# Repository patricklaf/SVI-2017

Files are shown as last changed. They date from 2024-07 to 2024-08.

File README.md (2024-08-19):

# SVI-2017

English - [Français](LISEZMOI.md)

The SVI-2017 board is the recreation of the interface board for the RobotArm SVI 2000.

The functional board in version 1.1 is compatible with MSX computers.

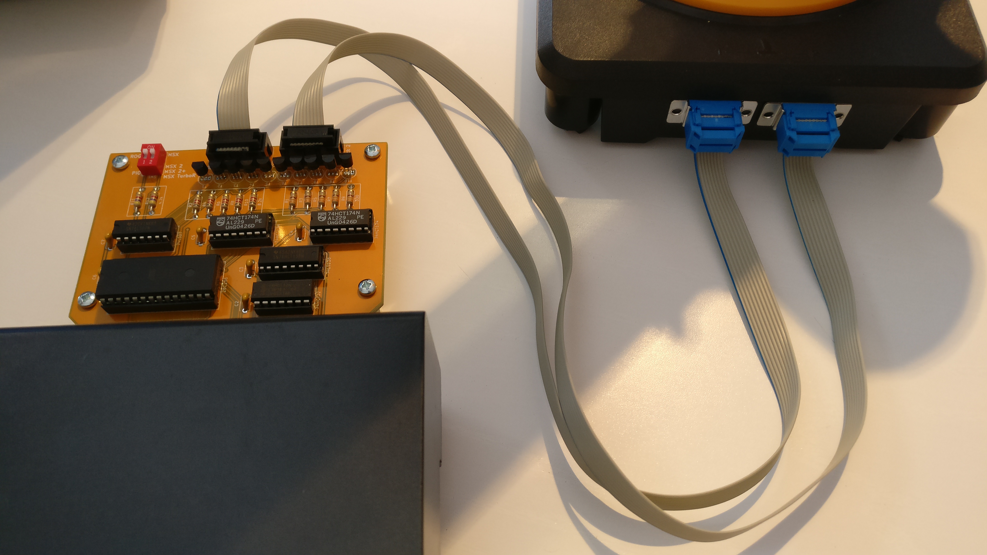
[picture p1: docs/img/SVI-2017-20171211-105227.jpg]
SVI-2017


## KiCad Project

The original project dates from 2017.

The [KiCad](KiCad/) folder contains the project migrated to KiCad 8.0.4.

The original archive [SVI-2017-201711091030.zip](https://github.com/patricklaf/SVI-2017/raw/main/KiCad/Gerber/SVI-2017-201711091030.zip) contains the Gerber files needed to produce the PCB. The build has been successfully tested by [Seeedstudio](https://www.seeedstudio.com/fusion_pcb.html).

An [interactive BOM](https://patricklaf.github.io/SVI-2017/bom.html) is available to view the list of required components and help with assembly.

You can order PCB directly from shared project on PCBWay.

<a href="https://www.pcbway.com/project/shareproject/SVI_2017_board_b98df38c.html">PCB from PCBWay</a>

## ROM

The [ROGO.ROM](https://github.com/patricklaf/SVI-2017/raw/main/ROM/ROGO.ROM) file is the image needed to program the EEPROM of the board.

The file combines the following elements:

- The ROGO ROM for MSX.
- The modified ROGO ROM for MSX 2, MSX 2+ and MSX TurboR.

## Usage

The DIP switch on the board selects the operating mode of the board.

Switch 1 selects the ROGO ROM or PIO mode.

Switch 2 selects the model of the computer used to activate the compatible ROM.

## ROGO

The ROGO language, similar to the Logo language, allows the robot to be controlled using commands.

A drawing of the robot on the screen reproduces the movements made.

## PIO

In PIO mode, the robot's movements are made by directly activating the motors, in one direction or another. Ports 0 and 1 are used. A movement is activated by setting the corresponding bit to 1. The movement stops when the bit is set to 0.

Port 0

| Bit | Movement |
|:---:|:---|
| 0 | Axis 2, arm forward |
| 1 | Axis 2, arm back |
| 2 | Axis 1, left rotation  |
| 3 | Axis 1, right rotation |
| 4 | Axis 5, clamp closing  |
| 5 | Axis 5, clamp opening  |

Port 1

| Bit | Movement |
|:---:|:---|
| 0 | Axis 3, arm down |
| 1 | Axis 3, arm up |
| 2 | Axis 1, clamp rotation left  |
| 3 | Axis 1, clamp rotation right |

> [!CAUTION]
> Never activate the 2 movements of an axis simultaneously, otherwise you risk damaging the electronics of the card.

## Acknowledgments

This project could not have been completed without the invaluable help of the members of the [MSX Village](https://msxvillage.fr) website.

There is a dedicated topic on the site's forum: [Robotarm SVI the diagram](https://msxvillage.fr/forum/topic-326-1+robotarm-svi-le-schema.php).

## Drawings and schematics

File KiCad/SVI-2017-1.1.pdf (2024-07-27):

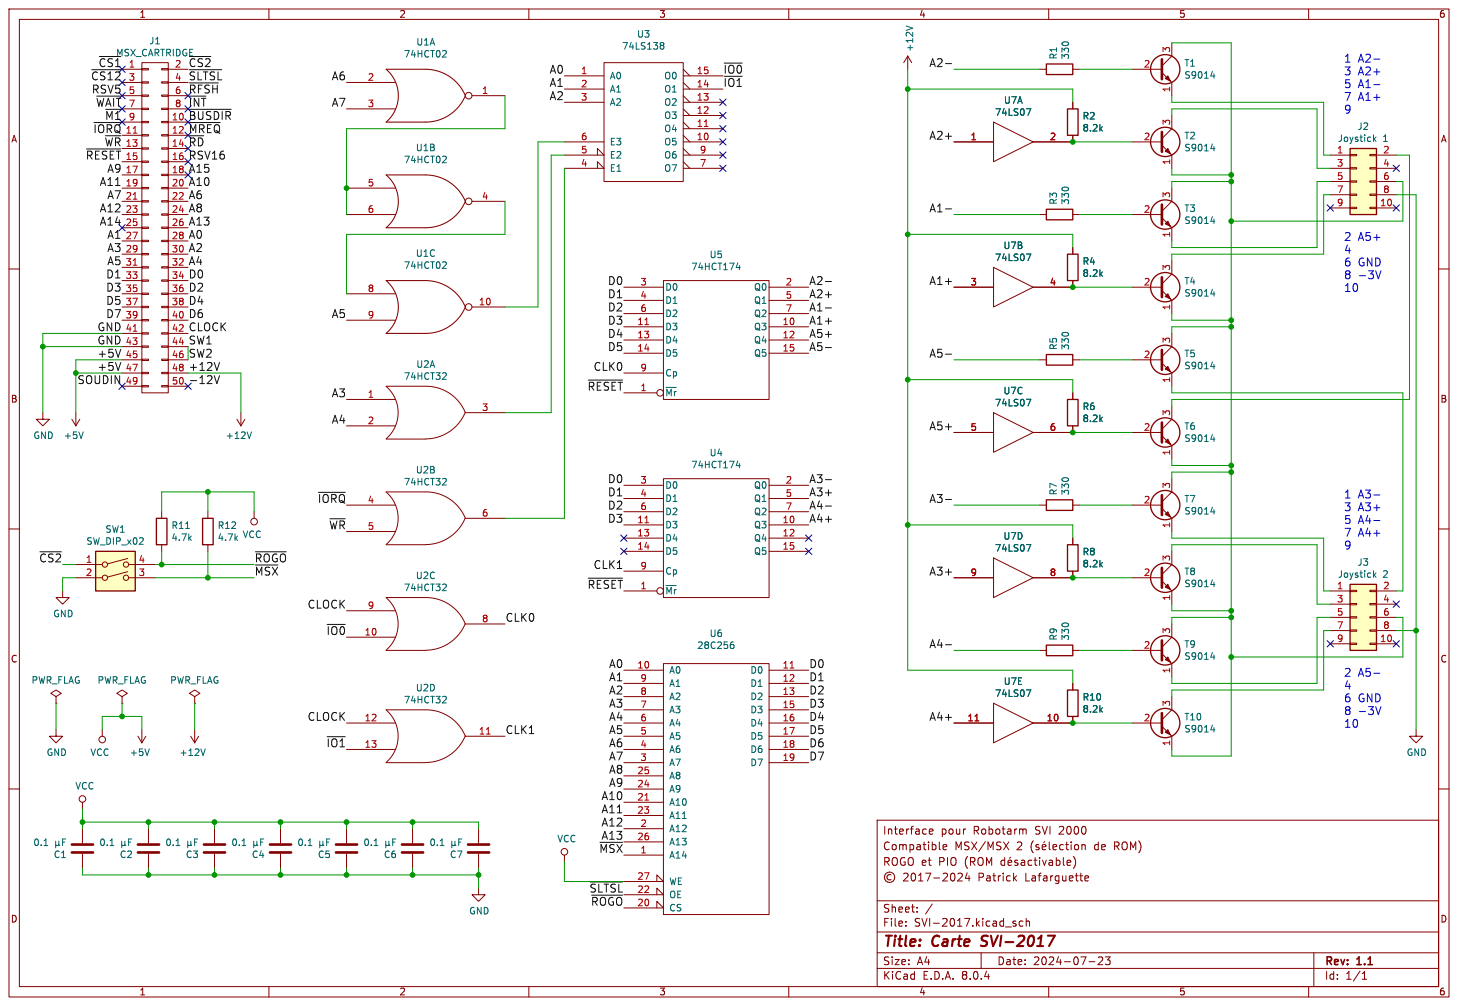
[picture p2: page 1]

Id: 1/1 Title: Carte SVI-2017

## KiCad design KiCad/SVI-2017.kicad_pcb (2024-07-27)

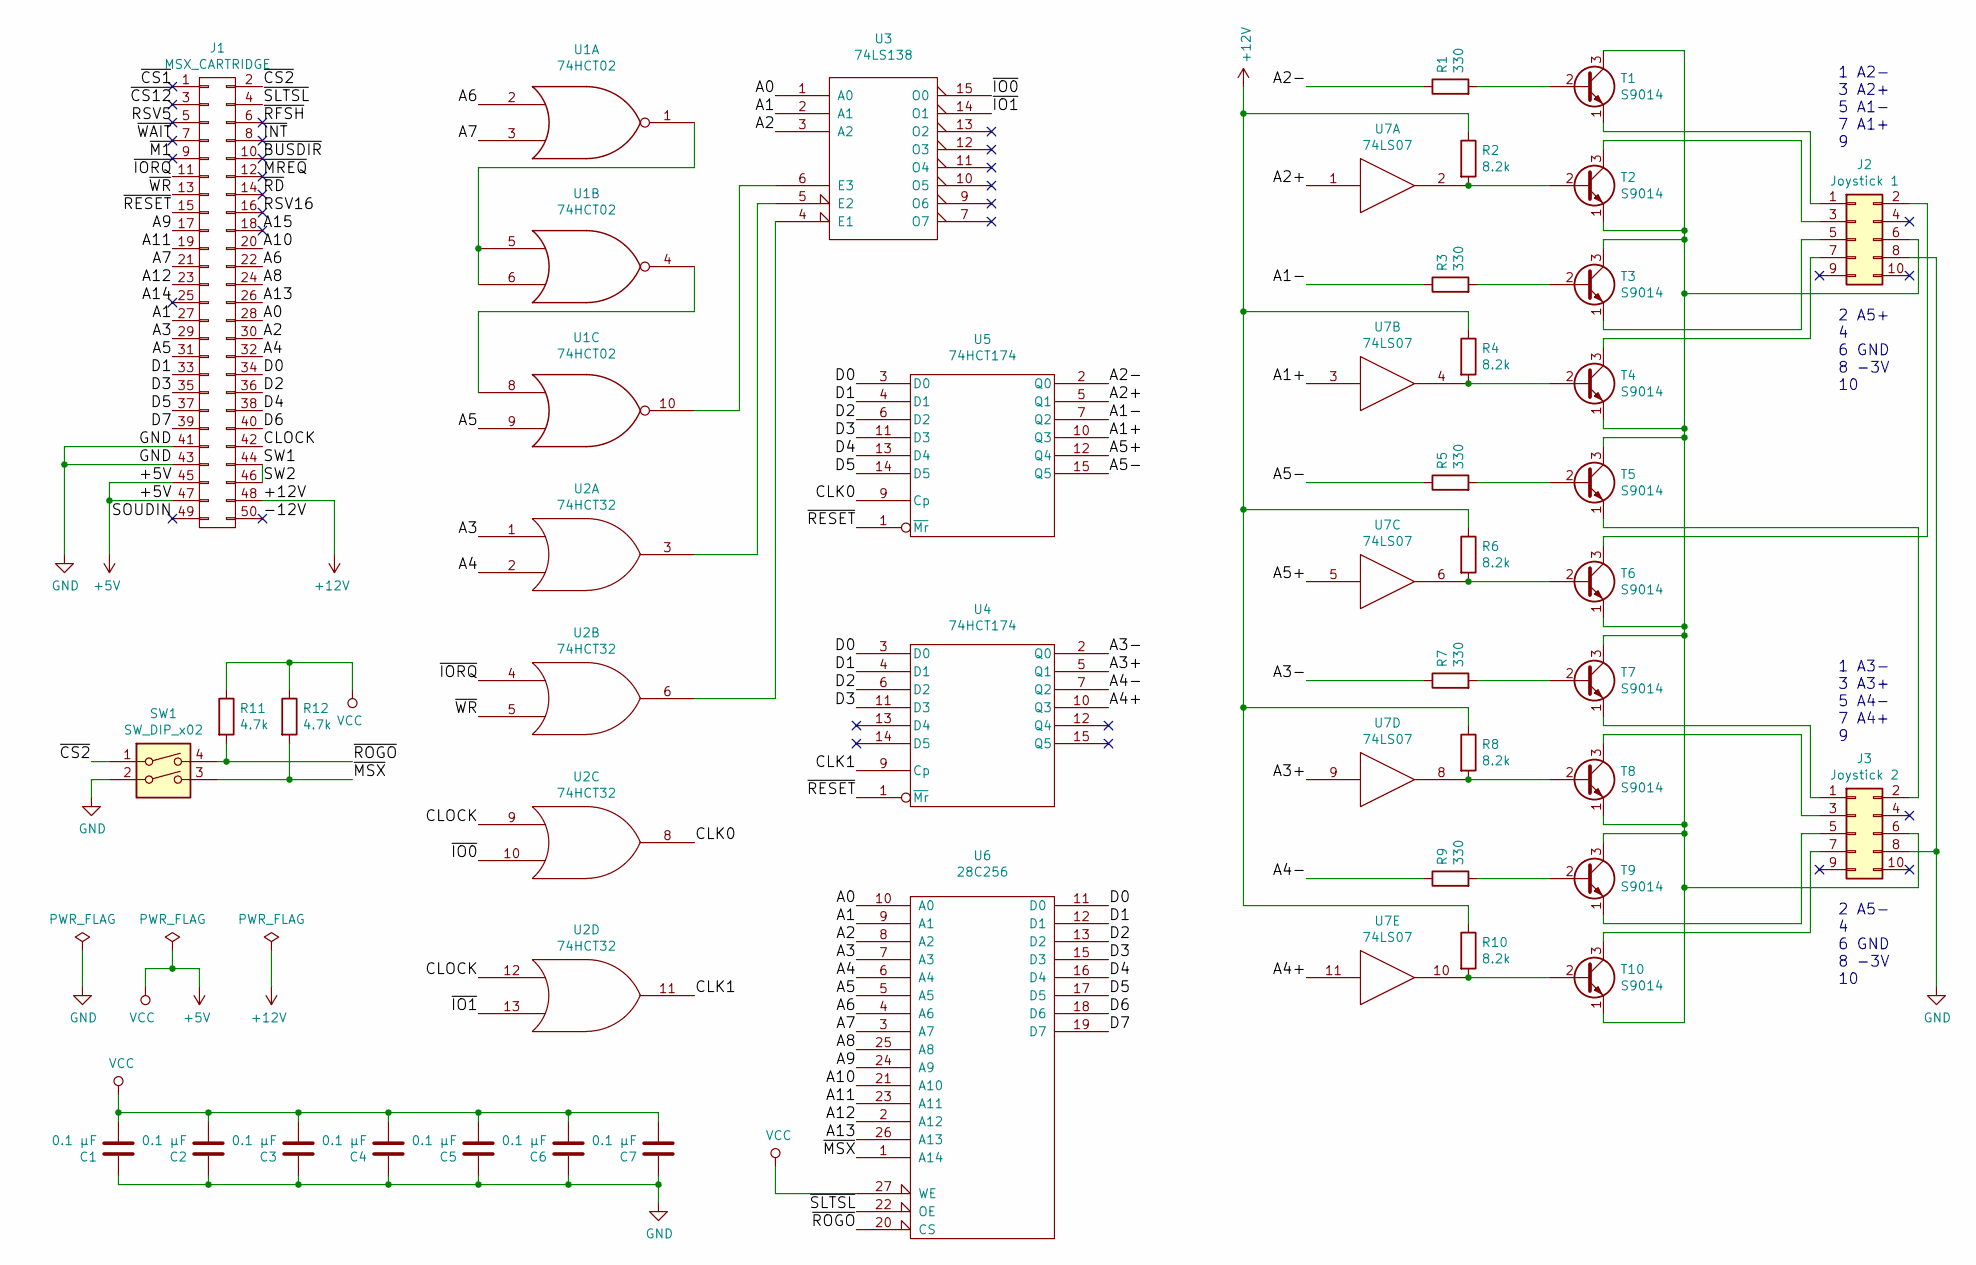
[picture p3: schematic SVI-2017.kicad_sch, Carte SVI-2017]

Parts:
C1, C2, C3, C4, C5, C6, C7: 0.1 µF; C_Disc_D5.1mm_W3.2mm_P5.00mm
J1: MSX_CARTRIDGE
J2: Joystick 1; IDC-Header_2x05_Pitch2.54mm_Straight
J3: Joystick 2; IDC-Header_2x05_Pitch2.54mm_Straight
R1, R3, R5, R7, R9: 330; R_Axial_DIN0207_L6.3mm_D2.5mm_P10.16mm_Horizontal
R2, R4, R6, R8, R10: 8.2k; R_Axial_DIN0207_L6.3mm_D2.5mm_P10.16mm_Horizontal
R11, R12: 4.7k; R_Axial_DIN0207_L6.3mm_D2.5mm_P10.16mm_Horizontal
SW1: SW_DIP_x02; SW_DIP_x2_W7.62mm_Slide
T1, T2, T3, T4, T5, T6, T7, T8, T9, T10: S9014; TO-92_Inline_Narrow_Oval
U1: 74HCT02; DIP-14_W7.62mm_Socket
U2: 74HCT32; DIP-14_W7.62mm_Socket
U3: 74LS138; DIP-16_W7.62mm_Socket
U4, U5: 74HCT174; DIP-16_W7.62mm_Socket
U6: 28C256; DIP-28_W15.24mm_Socket
U7: 74LS07; DIP-14_W7.62mm_Socket

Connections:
+5V: C1.2, C2.2, C3.2, C4.2, C5.2, C6.2, C7.2, J1.45, J1.47, R11.1, R12.1, U1.14 (VCC), U2.14 (VCC), U3.16 (VCC), U4.16 (VCC), U5.16 (VCC), U6.27 (WE), U6.28 (VCC), U7.14 (VCC)
+12V: J1.48, R2.1, R4.1, R6.1, R8.1, R10.1
/-12V: J1.50
/A0: J1.28, U3.1 (A0), U6.10 (A0)
/A1: J1.27, U3.2 (A1), U6.9 (A1)
/A1+: U5.10 (Q3), U7.3
/A1-: R3.1, U5.7 (Q2)
/A2: J1.30, U3.3 (A2), U6.8 (A2)
/A2+: U5.5 (Q1), U7.1
/A2-: R1.1, U5.2 (Q0)
/A3: J1.29, U2.1, U6.7 (A3)
/A3+: U4.5 (Q1), U7.9
/A3-: R7.1, U4.2 (Q0)
/A4: J1.32, U2.2, U6.6 (A4)
/A4+: U4.10 (Q3), U7.11
/A4-: R9.1, U4.7 (Q2)
/A5: J1.31, U1.9, U6.5 (A5)
/A5+: U5.12 (Q4), U7.5
/A5-: R5.1, U5.15 (Q5)
/A6: J1.22, U1.2, U6.4 (A6)
/A7: J1.21, U1.3, U6.3 (A7)
/A8: J1.24, U6.25 (A8)
/A9: J1.17, U6.24 (A9)
/A10: J1.20, U6.21 (A10)
/A11: J1.19, U6.23 (A11)
/A12: J1.23, U6.2 (A12)
/A13: J1.26, U6.26 (A13)
/A14: J1.25
/A15: J1.18
/CLK0: U2.8, U5.9 (Cp)
/CLK1: U2.11, U4.9 (Cp)
/CLOCK: J1.42, U2.9, U2.12
/D0: J1.34, U4.3 (D0), U5.3 (D0), U6.11 (D0)
/D1: J1.33, U4.4 (D1), U5.4 (D1), U6.12 (D1)
/D2: J1.36, U4.6 (D2), U5.6 (D2), U6.13 (D2)
/D3: J1.35, U4.11 (D3), U5.11 (D3), U6.15 (D3)
/D4: J1.38, U5.13 (D4), U6.16 (D4)
/D5: J1.37, U5.14 (D5), U6.17 (D5)
/D6: J1.40, U6.18 (D6)
/D7: J1.39, U6.19 (D7)
/RSV5: J1.5
/RSV16: J1.16
/SW1: J1.44, J1.46
/~BUSDIR: J1.10
/~CS1: J1.1
/~CS2: J1.2, SW1.1
/~CS12: J1.3
/~INT: J1.8
/~IO0: U2.10, U3.15 (O0)
/~IO1: U2.13, U3.14 (O1)
/~IORQ: J1.11, U2.4
/~M1: J1.9
/~MREQ: J1.12
/~MSX: R12.2, SW1.3, U6.1 (A14)
/~RD: J1.14
/~RESET: J1.15, U4.1 (~Mr), U5.1 (~Mr)
/~RFSH: J1.6
/~ROGO: R11.2, SW1.4, U6.20 (CS)
/~SLTSL: J1.4, U6.22 (OE)
/~WAIT: J1.7
/~WR: J1.13, U2.5
GND: C1.1, C2.1, C3.1, C4.1, C5.1, C6.1, C7.1, J1.41, J1.43, J2.8, J3.8, SW1.2, U1.7 (GND), U2.7 (GND), U3.8 (GND), U4.8 (GND), U5.8 (GND), U6.14 (GND), U7.7 (GND); also elsewhere on the board
unnamed: J2.1, T1.1 (E)
unnamed: J2.2, T6.3 (C)
unnamed: J2.3, T2.3 (C)
unnamed: J2.5, T3.1 (E)
unnamed: J2.6, J3.6, T1.3 (C), T2.1 (E), T3.3 (C), T4.1 (E), T5.3 (C), T6.1 (E), T7.3 (C), T8.1 (E), T9.3 (C), T10.1 (E)
unnamed: J2.7, T4.3 (C)
unnamed: J3.1, T7.1 (E)
unnamed: J3.2, T5.1 (E)
unnamed: J3.3, T8.3 (C)
unnamed: J3.5, T9.1 (E)
unnamed: J3.7, T10.3 (C)
unnamed: R1.2, T1.2 (B)
unnamed: R2.2, T2.2 (B), U7.2
unnamed: R3.2, T3.2 (B)
unnamed: R4.2, T4.2 (B), U7.4
unnamed: R5.2, T5.2 (B)
unnamed: R6.2, T6.2 (B), U7.6
unnamed: R7.2, T7.2 (B)
unnamed: R8.2, T8.2 (B), U7.8
unnamed: R9.2, T9.2 (B)
unnamed: R10.2, T10.2 (B), U7.10
unnamed: U1.1, U1.5, U1.6
unnamed: U1.4, U1.8
unnamed: U1.10, U3.6 (E3)
unnamed: U2.3, U3.5 (E2)
unnamed: U2.6, U3.4 (E1)

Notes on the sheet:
2 A5- 4 6 GND 8 -3V 10
1 A2- 3 A2+ 5 A1- 7 A1+ 9
1 A3- 3 A3+ 5 A4- 7 A4+ 9
2 A5+ 4 6 GND 8 -3V 10

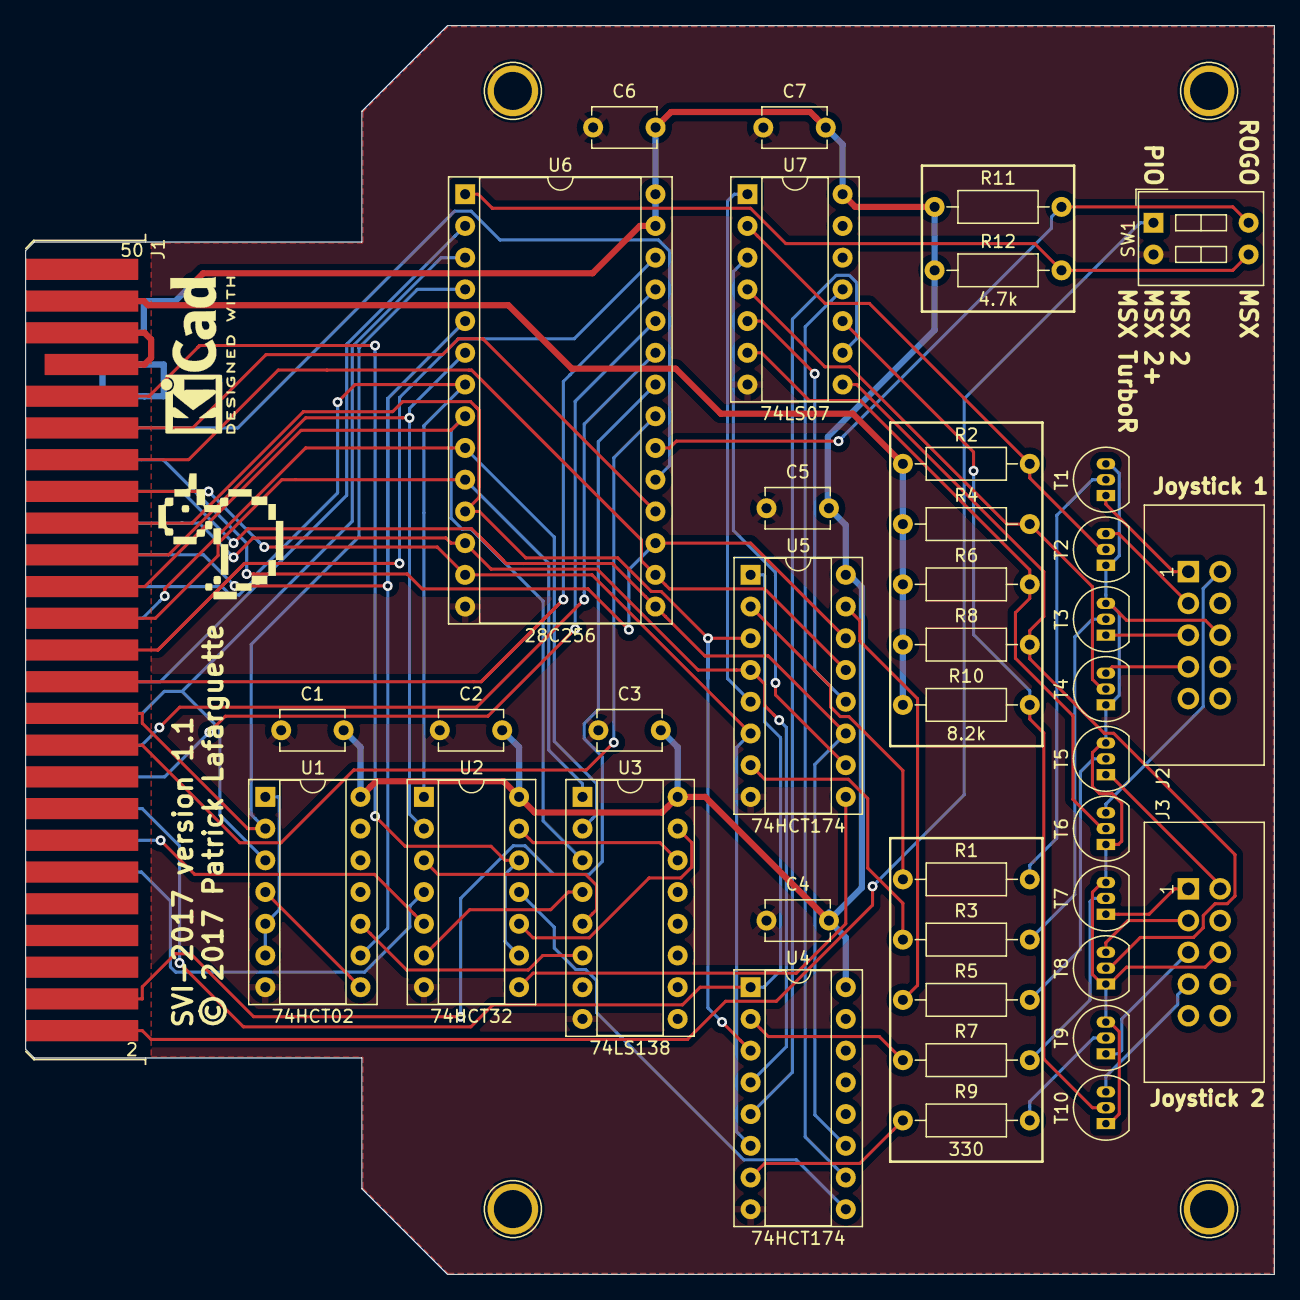
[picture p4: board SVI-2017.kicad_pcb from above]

Board: 2 copper layers, 100.0 x 100.0 mm, 46 parts (0 on the bottom side), 74 nets.

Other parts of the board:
BL: 1pin
BR: 1pin
COINCOIN: LOGO; COINCOIN
KICAD: KiCad-Logo2_12mm_SilkScreen; KiCad-Logo2_6mm_SilkScreen
TL: 1pin
TR: 1pin

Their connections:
GND: BL.1, BR.1, TL.1, TR.1; also elsewhere on the board

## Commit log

2024-07-27 Ajout du projet KiCad
    [SVI-2017.kicad_pcb, SVI-2017.kicad_sch]
2024-07-29 Modification du fichier README.
    - Ajout d'une photographie.
    - Ajout du fichier ROM.
    - Ajout des sections ROM, utilisation, ROGO et PIO.
2024-08-19 Correction d'un nom de fichier
2024-08-19 Passage de README.md en langue anglaise et ajout de LISEZMOI.md toujours en français
2024-08-19 Correction du lien vers la ROM pour permettre le téléchargement direct
2024-08-19 Ajout du lien vers PCBWay

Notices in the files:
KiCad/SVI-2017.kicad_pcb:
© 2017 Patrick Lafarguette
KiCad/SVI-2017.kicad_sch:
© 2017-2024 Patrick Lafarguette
